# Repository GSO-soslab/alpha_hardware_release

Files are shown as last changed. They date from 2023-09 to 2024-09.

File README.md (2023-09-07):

## ALPHA HARDWARE RELEASE
This repository provides design files for ALPHA AUV hardware.
- `Electronics` folder contains KiCad PCB files, documentations and guides.
- `CAD` folder contains CAD files for the mechanical parts.

**License: CERN-OHL-S-2.0**

**Funding:** NSF Award #2221676, #2238168 and #2154901

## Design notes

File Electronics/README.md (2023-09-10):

# ALPHA Hardware Repositority

The ALPHA Eletronics Hardware design is released under  [CERN-OHL-S-2.0](https://ohwr.org/cern_ohl_s_v2.txt) Licence
## **Introduction**

The most recent update:

- `sbc_hat` is a expansion board for single-board computers. It contains 8 RS232 ports (4 selectable between UART and RS232), 2 I2C buses, 2 ADC channels, and 5 direct GPIO connections. PDF schematics is available [here](https://github.com/GSO-soslab/alpha_hardware_release/blob/main/Electronics/doc/Schematics/sbc_hat.pdf)

- `thruster_driver` is a breakout board for MCU (MicroMod RP2040). This board is designed for interface with ESCs to control the thruster and servos. The voltage sensing capability is available (using a voltage devider) to monitoring the voltage to the thrusters. Communication ports are I2C, RS232 and RS485. Two additional GPIO is available for Digital Output fucntion. PDF schematics is available [here](https://github.com/GSO-soslab/alpha_hardware_release/blob/main/Electronics/doc/Schematics/thruster_driver.pdf)
 
- `Battery management` is a breakout board that uses diodes to allow battery pack parallization upto 4 packs. **IMPORTANT: You cannot charge batter packs from the Vout port on the board**

- `alpha_power_distribution_board` is a breakout board for distributing power sources for different devices on the ALPHA. You can plug in Pololu DC/DC circuit on the board with a 90 degree angled pin headers. A PDF schematics is available [here](https://github.com/GSO-soslab/alpha_hardware_release/blob/main/Electronics/doc/Schematics/alpha_power_distribution.pdf)

The detailed hardware information is available in the following links for users.
- [PI setup guide](https://github.com/GSO-soslab/alpha_hardware_release/blob/main/Electronics/doc/PI_setup_guide.md): This document provide information on how to configure the chips on the sbc_hat PBC.

- [`sbc_hat`](https://github.com/GSO-soslab/alpha_hardware_release/blob/main/Electronics/doc/SBC_HAT.md)

- [`thruster_driver`](https://github.com/GSO-soslab/alpha_hardware_release/blob/main/Electronics/doc/Thruster_driver.md)

- [`alpha_power_distribution_board`](https://github.com/GSO-soslab/alpha_hardware_release/blob/main/Electronics/doc/Alpha_power_distribution.md).

- [`Battery management`](https://github.com/GSO-soslab/alpha_hardware_release/blob/main/Electronics/doc/Battery_management.md)

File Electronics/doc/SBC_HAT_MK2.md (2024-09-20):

Pending update

## **SBC HAT MK2**
This board was originally design to be connected to a Raspberry PI 4.
However, it should also work with other SBCs with the same GPIO pin arrangement, e.g., Nvidia Jetson SBCs.

### RS232
All the pin functinos for the connectors are indicated on the PCB.

  To enable the I2C to UART chips, you need to edit `/boot/firmware/config.txt` file by adding the following lines.
  
  ```
#RS232 1&2 
dtoverlay=sc16is752-i2c,int_pin=23,addr=0x48
  ```

### ADC ports
Pin 1&2: A0
Pin 3&4: A1
The Voltage input are stepped down using a pair of resitors of 100k and 10k.

### PWM channels
We have 15 PWM channel exposed from the `PCA9685PW` chip. 
ROS driver of the chip can be found [here](https://github.com/uri-ocean-robotics/mvp_hardware_drivers/tree/noetic-devel/pwm_driver).

***Note***
The actual PWM signal generated by the chip maybe slightly off.
We suggest to use a oscilliscope to measure the PWM output.
You can tune the `pwm_ms_bias` parameter to offset the pwm signal to match the number you commanded.

### GPIO
WE have exposed 8 GPIO pins from the PI4.
GPIO7,8,9,10,11,12,13,16
We have a driver based on wiringPi to control the GPIO [here](https://github.com/uri-ocean-robotics/mvp_hardware_drivers/tree/noetic-devel/mvp_gpio_manager)

***Note1:***
The gpio param in the driver is based on the WiringPi pin map.
GPIO7 = 11
GPIO8 = 10
GPIO9 = 13
GPIO10 = 12
GPIO11 = 14
GPIO12 = 26
GPIO13 = 23
GPIO16 = 27

***Note2:***
You can program the gpio initial state to low by adding the commands in `/boot/firmware/config.txt`
```
gpio=13=op,dl
```
where `13` is the GPIO number (not the WiringPi number).

***Note3:***
Continous command from PI is not needed. The PWM will hold the PWM signal based on the last received command.

### MCU
We have a place for soldering a ATtiny85-20P MCU.
The MCU's I2C bus is connected to the PI's I2C, and `PB1` is connected to the `Enable` Pin of the PWM chip.
This allows user to implement safety feature to let MCU to turn off the PWM chip when no data is transmitted from PI to MCU.

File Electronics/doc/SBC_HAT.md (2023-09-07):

## **SBC HAT**
This board was originally design to be connected to a Raspberry PI 4.
However, it should also work with other SBCs with the same GPIO pin arrangement, e.g., Nvidia Jetson SBCs.

All the pin functinos for the connectors are indicated on the PCB.

  To enable all 4 I2C to UART chips, you need to edit `config.txt` file by adding the following lines.
  
  ```
#RS232 1&2 
dtoverlay=sc16is752-i2c,int_pin=23,addr=0x48
#RS232 3&4
dtoverlay=sc16is752-i2c,int_pin=24,addr=0x4C
#RS232 5&6 
dtoverlay=sc16is752-i2c,int_pin=25,addr=0x49
#RS232 7&8
dtoverlay=sc16is752-i2c,int_pin=22,addr=0x4D
  ```
  The port and connector index is listed below

  J14 = ttySC6

  J15 = ttySC7
  
  J9 = ttySC4
  
  J10 = ttySC5
  
  J4 = ttySC2
  
  J5 = ttySC3
  
  J8 = ttySC1
  
  J7 = ttySC0

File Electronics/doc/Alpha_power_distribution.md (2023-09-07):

## **ALPHA Power distribution board**

This board is designed to distribute the input voltage for different systems on the ALPHA AUV.
- The terminal blocks are rated at 16A. This is good for thrusters, input battery lines, and other high current draw sensors.
- The JST-XH connector are rated at 3A. This is designed for mid-low power sensors. 
- There are several JST-XH outputs 5v and 12v as indicated on the board. 
   - `5V3`, `5V2` and `5V1` obtains 5V power from different `D36V28F5` DC/DC regulator (5-50v input range with a max current rating of 3.2A) 
   - `12v` ports obtain power from a `D36V50F12` (5-50v input range with a maximum current rating of 4.5A)
   - Qwiic connector pins are connected to the enable pin of the `D36V50F12`, `D36V28F5`. 
      - Pin 1 controls 5V1 from U1
      - Pin 2 controls 5V2 from U2
      - Pin 3 controls 5V3 from U3
      - Pin 4 controls 12V from U4

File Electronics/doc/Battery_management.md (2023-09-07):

## **Battery power distribution board
This board is used to parallelize upto four battery packs to supply continuous energy for the ALPHA.

- Two rectifier diode arrays can be soldered (1 pair common cathode). We recommend to use `FERD60H100CGY-TR` which is rated at 100 V at 30A per diode. Or you can use `RB238NS150FHTLCT-ND` which is rated at 150v at 20A per diode.
- The diodes allows us to parallel multiple packs without charge each other. However, the downside is that only one battery pack (with the highest voltage) is supplying the energy to the overall system. Therefore, you need make sure the following things:
   - The battery's maximum discharge current rating is enough for your system
   - Your wiring for each battery is sufficient for carrying all the current.
- All the pads on the top layer are Positive pin of the battery or the output power. VB1 to VB4 pads are enlarged to allow two wires to be soldered on each pad. One wire connects to the battry, one wire connects to the charger.
- All the pads on the bottom layer are GND pads.

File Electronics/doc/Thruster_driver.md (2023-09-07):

## **Thruster driver board**
  ### Power input
  - The board can only be powered by 3.3v at `J8`
  
  ### Programming the MicroMod RP2040
  - Connect the two pins at `J11` to set the board to the boot mode before powering the system and connect the USB cable at `J10` 
  - Getting started document can be found [here](https://datasheets.raspberrypi.com/pico/getting-started-with-pico.pdf)
  - RP2040 SDK is can be found in [pdf](https://datasheets.raspberrypi.com/pico/raspberry-pi-pico-c-sdk.pdf) or [web](https://raspberrypi.github.io/pico-sdk-doxygen/)
  - Pin map of the MicroMod RP2040  can be found [here](https://learn.sparkfun.com/tutorials/micromod-rp2040-processor-board-hookup-guide), and pin map of RP2040 is available [here](https://datasheets.raspberrypi.com/pico/Pico-R3-A4-Pinout.pdf)
  - The actual Pin number for the PWM ports and the Serial ports are listed in the following section.
  - `J12` is used for reset the board.

  ### Building pico code inside the build/xx folder
  ```
      mkdir build
      cd build
      cmake ..
      make hello_pio
   ```

  ### Function ports
  - RS232-1 (4pin JST): the uart0 (GP0-TX, GP1-RX on RP2040) is converted into a RS232 port at `J7`. 
    - Pin1 (white bar): GND
    - Pin2: 3.3V from the power
    - Pin3: TX
    - Pin4: RX

 - RS232-2 (4pin JST): the uart1 (GP8-Tx, GP9-Rx on RP2040) into RS232 at `J2`. 
    - Pin1 (white bar): GND
    - Pin2: 3.3V from the power
    - Pin3: TX
    - Pin4: RX

 - I2C (4pin JST): The board has one I2C communication port at `J5`. 
    - Pin1: GND
    - Pin2: 3.3V
    - Pin3: SDA (GP04 on RP2040)
    - Pin4: SCL (GP05 on RP2040)

- PWM channels (4pin JST): The board has 6 PWM channels at `J3`, `J4` and `J6` for controlling ESC and servo motors.
    - Pin1&2: GND
    - Pin3&4: PWM signal
    - J3: P3->GPIO24->4A, P4->GPIO13->6B
    - J4: P3->GPIO18->1A, P4->GPIO16->0A
    - J6: P3->GPIO22->3A, P4->GPIO20->2A
    - These pins could be configured as regular GPIO as well.

- Voltage sensing (VB at `J8`). User could sense the input voltage at VB pin through a voltage divider (100k omh and 10k omh in serial). The divided voltage is connected to GPIO26(ADC0) on the RP2040.

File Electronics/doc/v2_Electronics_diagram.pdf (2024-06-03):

Power distribution board

VB

5V

12V

MCU
board
PWM | RS232
USB | Pi4 with HAT
Ethernet | RS232

I2C

ADC

VIN

VIN

VIN

LUMA_E

VIN

Current sensor Analog Out

MB switch

VIN Tether Tether board

ESC

VIN

PWM

Motor wires VIN

PWM

Motor wires VIN

PWM

Motor wires VIN

PWM

Motor wires

VB | VB Current through

5V

Ethernet FLS_3 Ping360_E

Doodle_E

Ethernet

5V

VB

VB

VB

Surge¹ | VB

Sway¹,2

HS¹,2

# HB¹,2 Vin

Acomm

# WIFI GPS Tether

Ping
360³

Bar30

DVL³

FLS³

VB

VB

24v

24v

3 pin | 4 pin

6 pin Hybrid New

6pin
hybrid
old

8 pin
old

8 pin New

Note 1: All thruster should use the same blade direction. And the motor wiring has to be confirmed such that PWM >1500 will generate thrust towards the cable side (air pushing through the thruster). Note 2: T200 Thrusters on ALPHA RISE uses 3pin-power connector, which is thicker than the regular BT 3pin connector Note 3: All ethernet port are powered by VB unless further described. Note 4: Dotted line means additional devices

# PWM0 PWM1 PWM2 PWM3

VB

RS232-1

ttySC3
J5
J4/ttySC2 Ethernet Standard BT Bulkhead connector wiring 1 | RX+ 2 | RX- 3 | TX+ 4 | Vcc 5 | GND 6 | TX- 78 | Serial RX or IO
Cable (Female) | Bulkhead (Male) | Tether 1 | NC 2 | NC 3 | NC 4 | + 5 | - 6 | NC 7 | NC 8 | NC | 1 | D1- 2 | D1+ 3 | D2- 4 | D3+ 5 | D3- 6 | D2+ 7 | 5V 8 | GND Triple USB (Old Fin) 1 | D1- 2 | D1+ 3 | 5V2 4 | D2+ 5 | D2- 6 | 5V1 7 | GND2 8 | GND1
Double USB (WIFI+GPS Fin)
Ethernet 1 | GND 2 | VCC 3 | RX+ 4 | RX- 5 | TX+ 6 | TX-

## Bulkhead (Male)

Serial TX or IO

Cable (Female) | 1 | GND 2 | 5V 3 | D- 4 | D+ 5 | D- 6 | D+
Double USB (WIFI+GPS Fin) | 1 | GND 2 | 5V 3 | D- 4 | D+ 5 | SBC_RX 6 | SBC_TX

USB + RS232

Cable (Female) | Bulkhead (Male) | RS232 1 | GND 2 | VCC 3 | SBC_RX 4 | SBC_TX
Main power 1 | GND 2 | VB 3 | GND 4 | VB
Battery power (customized with BR 12 AWG Power cable) 1 | GND 2 | GND 3 | VB 4 | VB
Servo/LED 1 | GND 2 | VCC 3 | PWM
Cable (Female) | Bulkhead (Male)

Double USB Main power Tether

Ethernet

Ethernet

Ethernet

RS232

Battery1

Battery2

Battery3

Battery4

Dual diode

Dual diode

Battery power

Battery power

Battery power

Battery power

VIN | GND
Main power 1 | GND 2 | 5V 3 | D- 4 | D+ 5 | NC 6 | Sync (optional)

Single USB

## Battery management diagram

## Electronics housing

## 12A rated per pin

## 20A rated per pin

## 20A (P1 & P2) 3A (P3-P6)

## 3A per pin

## Connector color code

VIN Tether_E

GB Switch

Ethernet

Jetson E

DVL_E

PI_E

VB

LUMA³

Long
range WIFI³

Jetson Ethernet USB

USBX2

USB Camera USB

3.0

PWM | LED

VIN

PWM

Motor wires

VIN

PWM

Motor wires

Thruster
/Servo

Thruster
/servo

12v 12v

30 A rated per channel

6pin
regular

GPIO13

ADC1

ADC0 1 | NC 2 | SSTX+ 3 | SSTX- 4 | SSRX+ 5 | SSRX- 6 | D+ 7 | D- 8 | NC

USB3

Cable (Female) | Bulkhead (Male) | 1 | GND 2 | 5V 3 | Pri Exposure 4 | Pri Trigger 5 | Sec Power 6 | Sec. Exposure

FLIR Cam
power +trigger

VIN

12v

DVL_E

LUMA-E 1 | B- 2 | B+ 3 | B1 4 | B3 5 | B2 6 | NC

BR 14.8V battery balance port

Latte Panda USB USB USB | IP | HDMI

Power

VIN

Ethernet

GB Switch

Ethernet

Ethernet

Ethernet

Ethernet

Internet

Router Ethernet VIN

Ethernet Acomm | USB

HDMI

Power bar VVVV | Power

USB Keyboard

Mourse

Long range WIFI

IP

Power

Internet

Antenna | Antenna

Front

Bottom Top
Back

Back

BackTop | Text Tether_E | Doodle_E | GPS

Antenna Tether board

TP-link N300

TP-link N300 | Laptop

Laptop

5km Tether port 1 | BLK-1 2 | RED-1 3 | Y-1 4 | BLK-2 5 | RED-2 6 | Y-2

ESC spliter

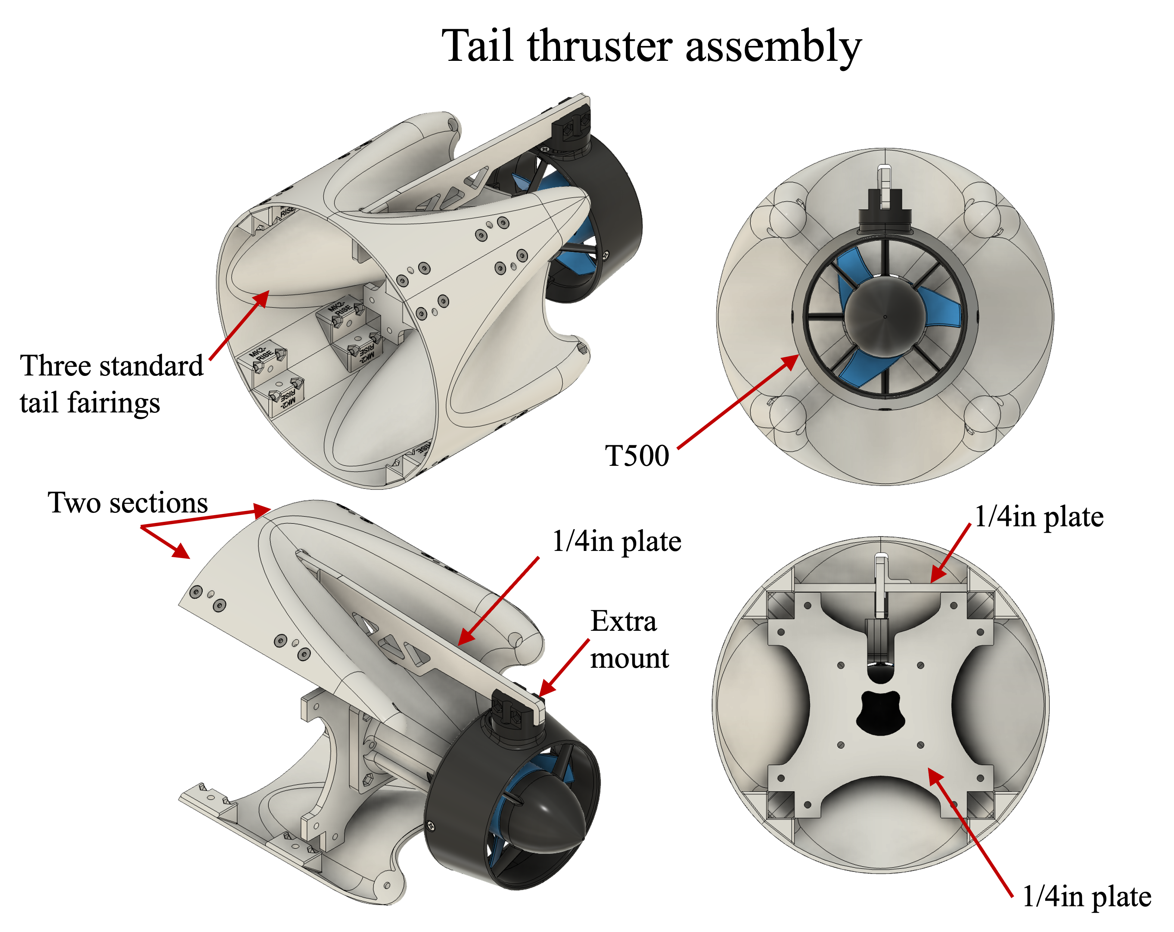
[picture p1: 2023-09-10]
CAD/Acutators/AC-AS-01-02.png

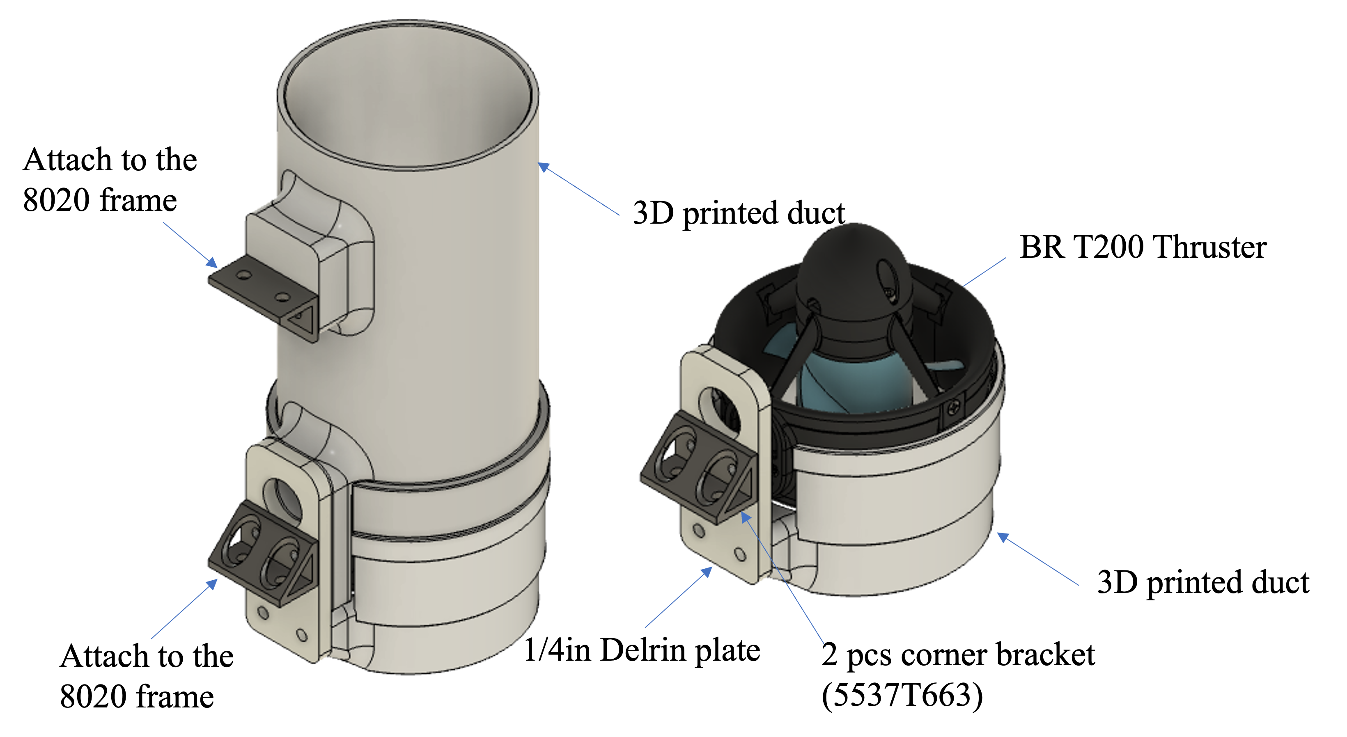
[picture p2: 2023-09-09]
CAD/Acutators/AC-AS-01-01.png

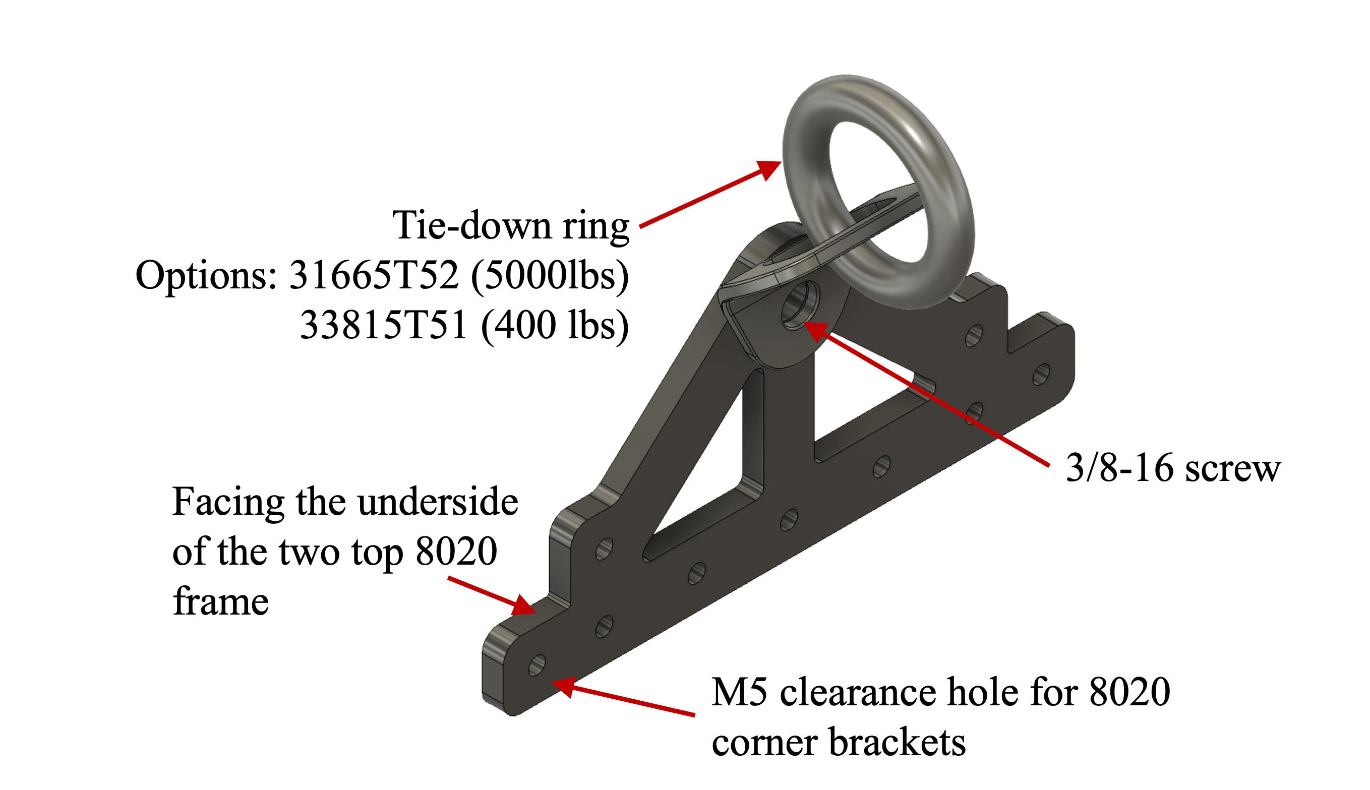
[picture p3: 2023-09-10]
CAD/Others/Lifting_plate_diagram.png

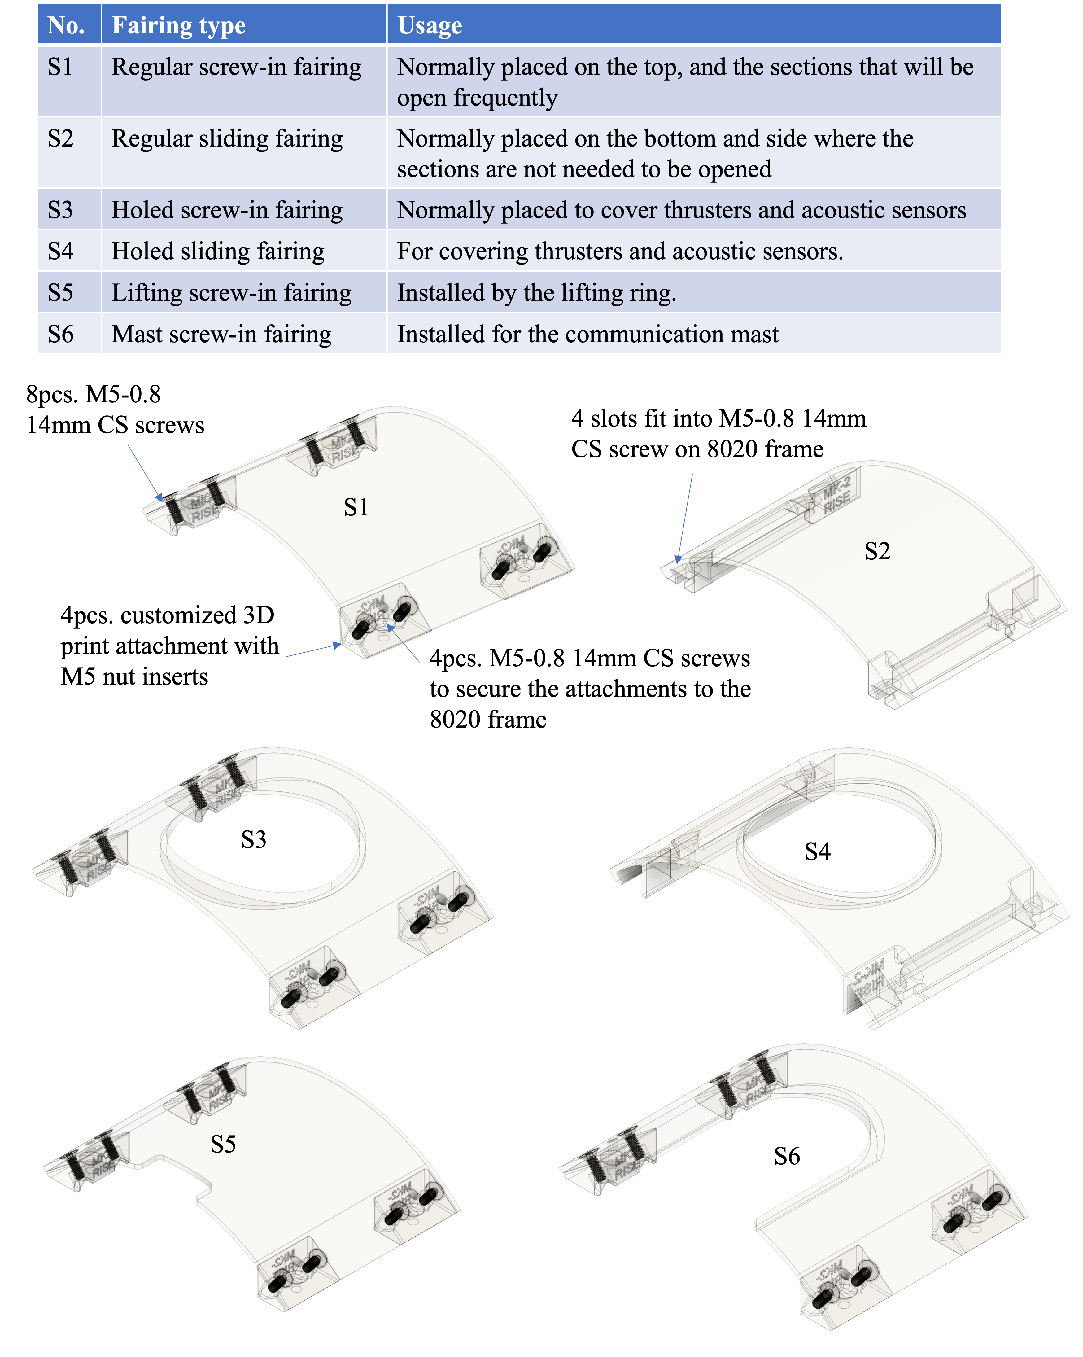
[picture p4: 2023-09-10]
CAD/Fairing/fairing_information.png

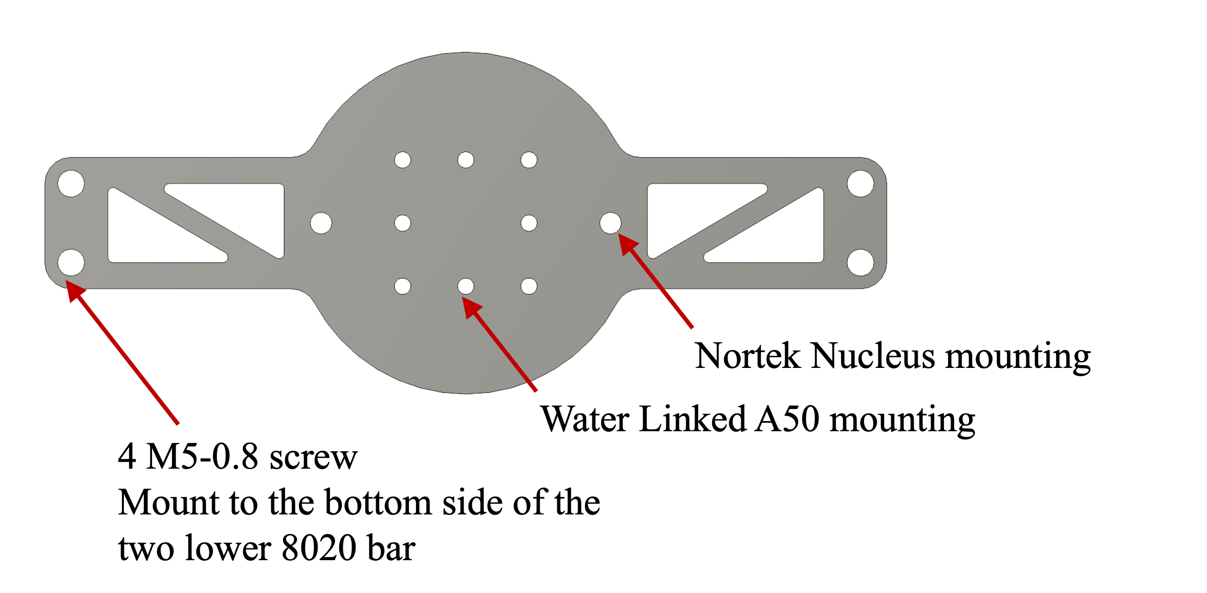
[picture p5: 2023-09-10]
CAD/Others/DVL_plate_information.png

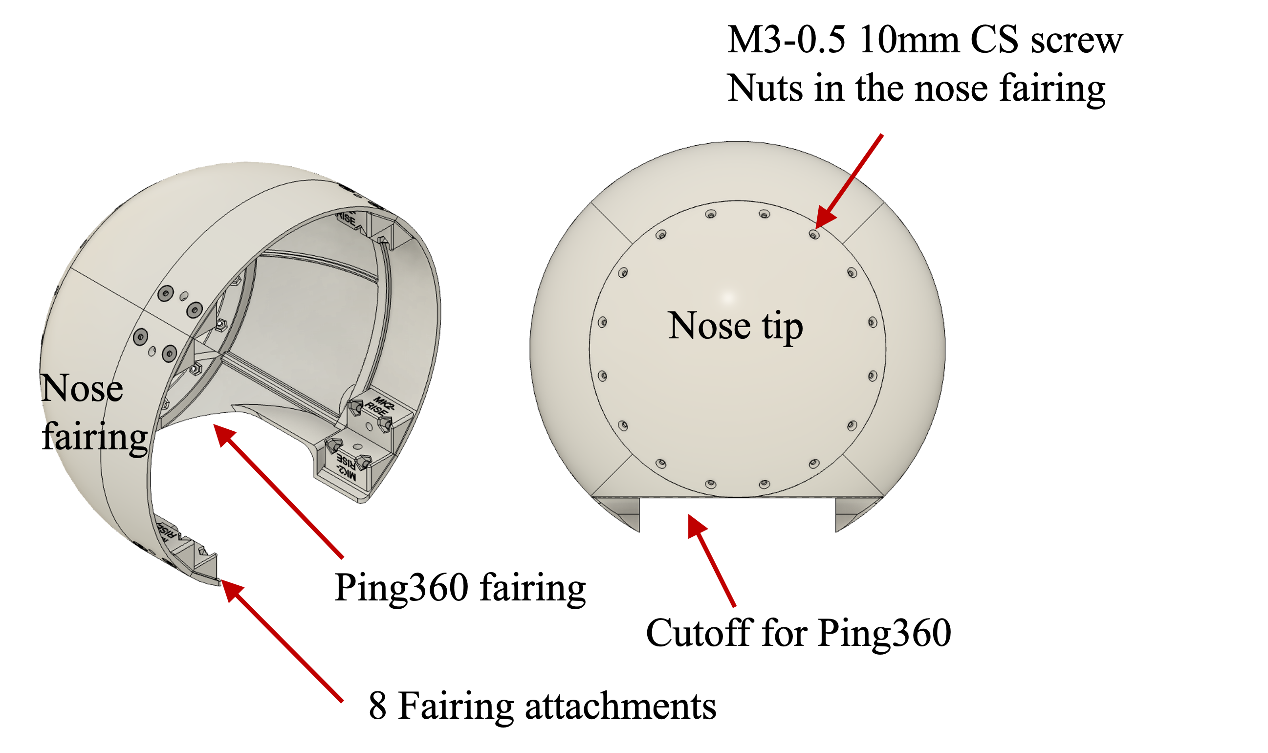
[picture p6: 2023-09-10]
CAD/Fairing/FA-AS-01-01.png

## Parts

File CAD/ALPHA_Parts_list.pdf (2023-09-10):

ALPHA Parts List

Part number explaination
XX-XX-XX-XX
1st and 2nd digits Category | BR-Blue Robotics, MC-McMaster Carr
3rd and 4th digits Assembly | External vendor uses vendor part number and description
5th and 6th digits | Assembly number
7th and 8th digits | Number | 00 means an assembly
Category | Part number | Description
Actuators (AC) | AC-AS-01-00 | Tunnel thruster assembly
Actuators (AC) | AC-AS-01-01 | Short tunnel
Actuators (AC) | AC-AS-01-02 | Long tunnel
Actuators (AC) | BR-T200 | Blue Robotics T200
Actuators (AC) | MC-5537T663 | T-slot corner bracket 2 holes
Actuators (AC) | AC-AS-02-00 | Surge thruster assembly
Actuators (AC) | AC-AS-02-01 | T500 Top mount
Actuators (AC) | AC-AS-02-02 | T500 Back mount
Actuators (AC) | AC-AS-02-03 | T500 Mounting plate
Actuators (AC) | AC-AS-02-04 | T500 hanging plate
Actuators (AC) | AC-AS-02-05 | T500 hanging cross
Actuators (AC) | BR-T500-R1 | Blue Robotics T500
Electronics (EL) | EL-AS-01-00 | Electronics housing assembly (4in aluminum Blue Robotics Housing)
Electronics (EL) | EL-AS-01-01 | Internal chasis end plate
Electronics (EL) | EL-AS-01-02 | Internal electronics mounting plate
Electronics (EL) | BR-STANDOFF | Blue Robotics M3 standoff 212 mm long
Fairing (FA) | FA-AS-01-00 | Nose cone fairing assembly
Fairing (FA) | FA-AS-01-01 | Nose fairing
Fairing (FA) | FA-AS-01-02 | Nose fairing for Ping360
Fairing (FA) | FA-AS-01-03 | Nose tip fairing
Fairing (FA) | FA-AS-02-00 | Tail cone fairing assembly
Fairing (FA) | FA-AS-02-01 | Tail cone fairing regular
Fairing (FA) | FA-AS-02-02 | Tail cone fairing top port
Fairing (FA) | FA-AS-02-03 | Tail cone fairing top starboard
Fairing (FA) | FA-AS-03-00 | Mid section fairing assembly
Fairing (FA) | FA-AS-03-01 | Screw-in fairing regular
Fairing (FA) | FA-AS-03-02 | Slide-in fairing regular
Fairing (FA) | FA-AS-03-03 | Screw-in fairing for thruster/DVL
Fairing (FA) | FA-AS-03-04 | Slide-in fairing for thruter/DVL
Fairing (FA) | FA-AS-03-05 | Screw-in fairing for lifting plate
Fairing (FA) | FA-AS-03-06 | Screw-in fairing for mast
Fairing (FA) | FA-00-01 | Screw-in fairing adapter
Frame (FR) | FR-AS-01-00 | ALPHA main frame
Frame (FR) | FR-AS-01-01 | Big middle frame 1/2in HDPE
Frame (FR) | FR-AS-01-02 | Small middle frame for holding housings 1/2in HDPE
Frame (FR) | FR-AS-01-03 | Special screw-in fairing adapter
Frame (FR) | MC-5537T935 | 20mm 8020 Corner bracket
Frame (FR) | MC-5537T518 | 20mm 8020 Corner bracket
Frame (FR) | MC-5537T514-4FT | 4ft long 20mm 8020
Stand (ST) | ST-AS-01-00 | AUV Stand Assembly
Stand (ST) | ST-AS-02-00 | Stand Arc assembly
Stand (ST) | ST-AS-01-01 | Arc plate
Stand (ST) | ST-AS-01-02 | 3D Printed Arc core side
Stand (ST) | ST-AS-01-03 | 3D Printed Arc core middle
Stand (ST) | MC-47065T107 | 1in by 2in 8020 3ft or 4ft long
Stand (ST) | MC-47065T101 | 1in by 1in 8020 6in long
Stand (ST) | MC-47065T663 | 1in 8020 corner bracket
Others (OT) | OT-AS-01-01 | DVL plate 1/4in thick Delrin
Others (OT) | OT-AS-02-01 | Lifting plate 1/4 in Aluminum
Others (OT) | MC-33815T51 | Lifting ring 400 lbs rated
Others (OT) | MC-31665T52 | Lifting ring 5000 lbs rated
Others (OT) | OT-AS-03-00 | Ping360 mounting assembly
Others (OT) | OT-AS-03-01 | Ping360 Plate 3/16in Delrin
Others (OT) | OT-AS-03-02 | Ping360 Spacer, 3D printed
Others (OT) | BR-Ping360 | Blue Robotics Ping360

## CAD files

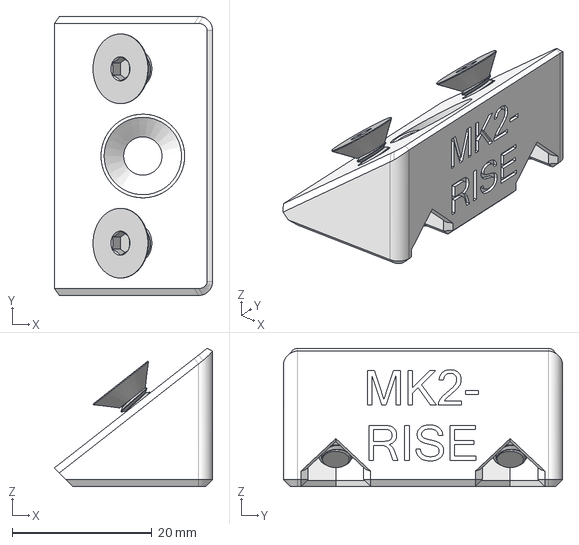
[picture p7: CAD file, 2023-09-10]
CAD/Fairing/Parts/FA-00-01.step
22.7 x 40.0 x 19.8 mm
92125A211_18-8 Stainless Steel Hex Drive Flat Head Screw x 2

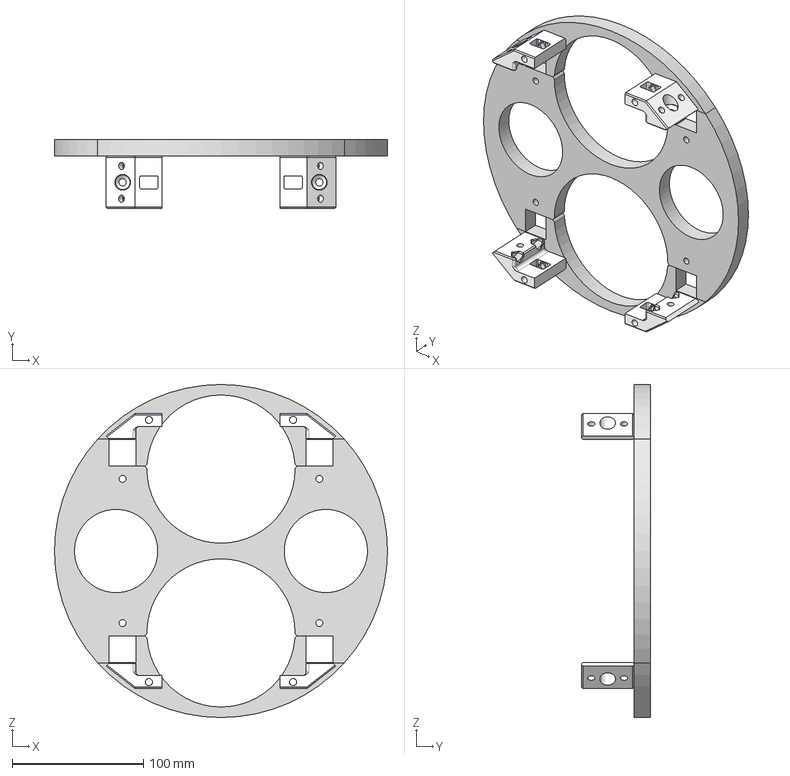
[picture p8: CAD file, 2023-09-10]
CAD/Frame/FR-AS-02-00.step
254.0 x 52.7 x 254.0 mm
FR-AS-01-01
FR-AS-01-02 x 2
FR-AS-01-03 x 2
FR-AS-01-03 v1(Mirror) x 2

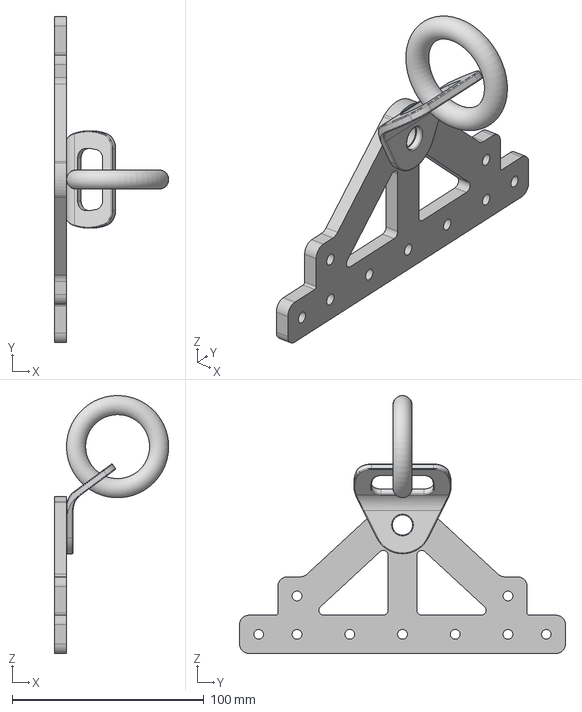
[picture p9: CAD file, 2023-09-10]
CAD/Others/Parts/OT-AS-02-00.step
59.7 x 170.0 x 134.5 mm
OT-AS-02-01
MC-31665T52

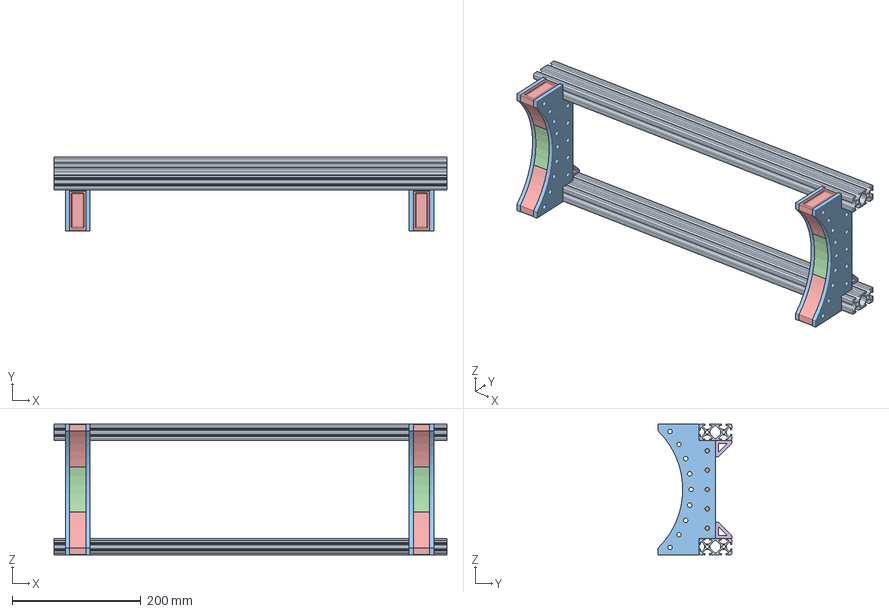
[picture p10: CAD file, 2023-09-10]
CAD/Stand/ST-AS-01-00 v2.step
609.6 x 114.3 x 203.2 mm
MC-47065T107 x 2
MC-47065T411_6in x 2
ST-AS-01-01 x 4
ST-AS-01-03 x 2
ST-AS-01-02 x 4
MC-47065T663 x 4

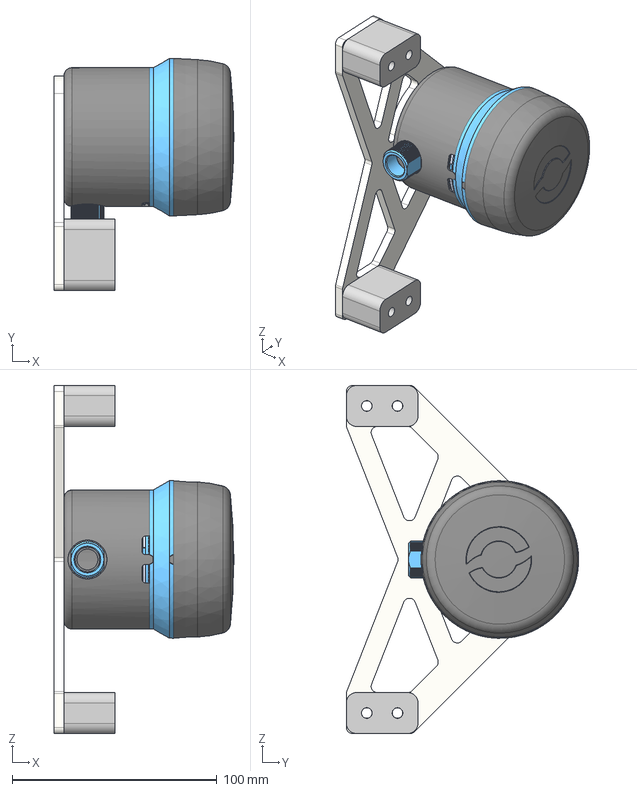
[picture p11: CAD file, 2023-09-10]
CAD/Others/Parts/OT-AS-03-00.step
87.8 x 113.5 x 170.0 mm
OT-AS-03-01
OT-AS-03-02 x 2
BR-Ping360

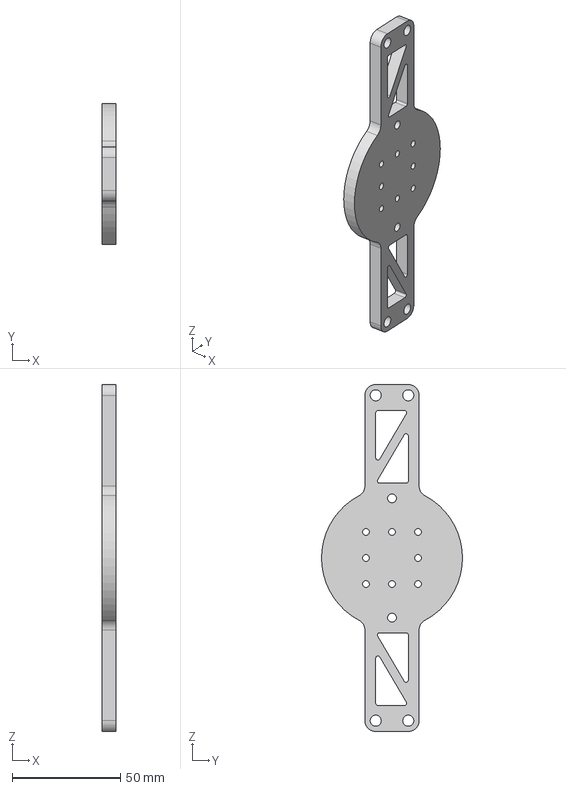
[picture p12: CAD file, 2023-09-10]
CAD/Others/Parts/OT-AS-01-01.step
6.35 x 65.0 x 160.0 mm

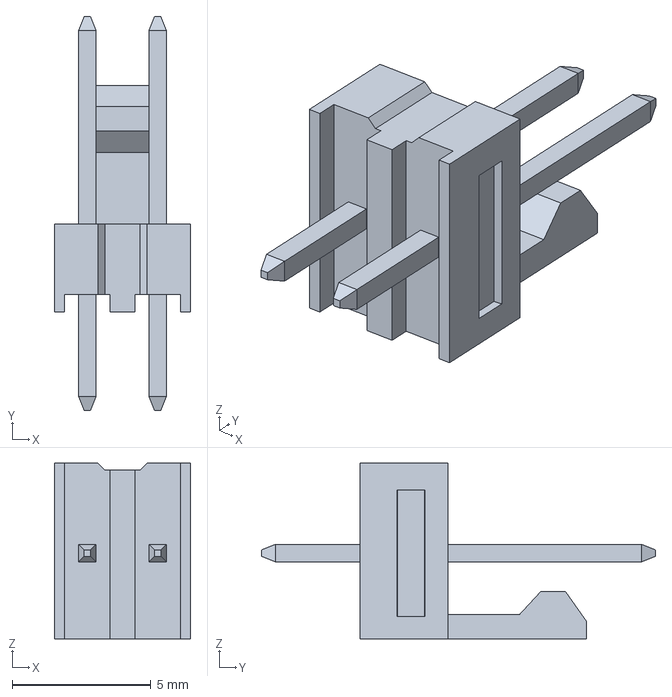
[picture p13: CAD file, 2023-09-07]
Electronics/sbc_hat_mk2/project_3dshapes/022232021.stp
4.93 x 14.2 x 6.35 mm

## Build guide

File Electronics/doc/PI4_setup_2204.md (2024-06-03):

### First-time boot-up setup (HDMI and keyboard needed)

- username: `mvp_admin`, password: `temppwd`

- `hostname -I` or `ip -a address` to check current IP
- Edit the netplan `sudo nano /etc/netplan/50-cloud-init.yaml`
- add `addresses: [192.168.1.124/24]`
- `ping google.com`
- Disable auto update `sudo dpkg-reconfigure -plow unattended-upgrades`

### Open I2C port

- `sudo apt update`
- `sudo apt install raspi-config`
- `sudo raspi-config`
- Go to `Interface Options` > `I2c` enable it
- Go to `Interface Opetions` > `SPI` disable it

### Setup I2C UART Chip (sc16is752-i2c)

- Install libraries

  ```
  sudo apt-get install -y make
  sudo apt-get install build-essential
  ```

  ```
  wget http://www.airspayce.com/mikem/bcm2835/bcm2835-1.71.tar.gz
  tar zxvf bcm2835-1.71.tar.gz 
  cd bcm2835-1.71/
  sudo ./configure
  sudo make
  sudo make check
  sudo make install
  #For more details, please refer to http://www.airspayce.com/mikem/bcm2835/
  ```

  ```
  sudo apt-get install python3-dev
  sudo apt-get install python3-rpi.gpio
  sudo apt-get install python3-smbus
  ```

- Add device using `dtoverlay`

  - `sudo nano /boot/firmware/config.txt`

  - add the following lines at the end

    ```
    #RS232 1&2 SC6, SC7
    dtoverlay=sc16is752-i2c,int_pin=23,addr=0x48
    #RS232 3&4 SC4, SC5
    dtoverlay=sc16is752-i2c,int_pin=24,addr=0x4C
    ##the last two is for the 8 RS232 version
    #RS232 5&6 SC2 SC3
    dtoverlay=sc16is752-i2c,int_pin=25,addr=0x49
    #RS232 7&8 SC0 SC1
    dtoverlay=sc16is752-i2c,int_pin=22,addr=0x4D
    ```

  - `sudo reboot`

- Check new serial ports

  - `ls /dev/ttySC*`

  - If you see SC0, SC1 ..... and so on, then you are good.

    | Connector | Dev    |
    | --------- | ------ |
    | J8        | ttySC0 |
    | J7        | ttySC1 |
    | J4        | ttySC2 |
    | J5        | ttySC3 |
    | J9        | ttySC4 |
    | J10       | ttySC5 |
    | J14       | ttySC6 |
    | J15       | ttySC7 |

  - Test with `minicom`

  - `sudo minicom -s`
    - `ctrl+A` then `o`: configure the port
    - `ctrl+A` then `x` : exit the program.

### GPIO conifguration 

On the hat we have 5 GPIOs (7,8, 9, 12, 13). We use the GPIO as output pins to control MOSFET and power supplies to control sensor payloads. GPIO9, 12, 13 can be configured as normal GPIO.

- First, you need to export the GPIO

```
echo 9 > /sys/class/gpio/export
```

- Second, you can set the direction of the GPIO

```
echo out > /sys/class/gpio/direction
```

- Finally, you can set the GPIO to High[1] or Low [0]

```
echo 1 > /sys/class/gpio/direction
```

***Note***: For GPIO7  and GPIO8, they are originally used as chip select pin for SPI in the PI system. To free them to become a regular GPIO, you need to add the  following line in `/boot/config.txt` and `/boot/firmware/config.txt` file after the line `dtparam=spi=off`. The added line will remapp the chip select pin to other GPIOs, i.e., 20 and 21 here. Then, you can reboot the PI, and `GPIO7` and `GPIO8` can be used as normal GPIOs.

```
dtoverlay=spi0-cs,cs0_pin=20,cs1_pin=21
```

### Install ROS Humble

[Reference](https://docs.ros.org/en/humble/Installation/Ubuntu-Install-Debians.html)

- add source bash into your ~/.bashrc 

- only install the base `sudo apt install ros-humble-ros-base`

- install the demo_node packages to test ros 

  ```
  sudo apt install ros-humble-demo-nodes-cpp
  sudo apt install ros-humble-demo-nodes-py
  ```

### Test ADC chip (MCP3422)

### Test Bar30 pressure sensor

### Test XSense MTI 

## PWM Driver add-on Board

### Configure Real-time clock (DS3231)

- Install `i2c-tools`
- `i2cdetect -y 1` to scan the device on the i2c bus and get their address
- scan the port make sure the devices are there.
- The I2C address of the clock should be `0x68`

[Reference](https://learn.adafruit.com/adding-a-real-time-clock-to-raspberry-pi/set-up-and-test-i2c)

### Configure the PWM chip (PCA9685)

- The I2C address should be `0x40` and `0x70`, the later one is the default all channel address.

## Install MVP Framework

### MVP messages

### MVP Control

### MVP Mission

### MVP Core (ALPHA_core for ROS Noetic)

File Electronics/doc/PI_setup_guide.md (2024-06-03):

# PI setup guide for the ALPHA RISE SBC HAT
## Create Ubuntu 20.04 image.
- Open **Raspberry Pi Imager** 
- Choose **Other general-purpose OS** 
- Select **Ubuntu**
- Scroll down **Ubuntu Server 20.04.5 LTS(64-bit)** option
- Click the Advanced options icon at the right-bottom corner
    - Check **Set hostname**
    - Check **Enable SSH**, select **Use password authentication**
    - Check **Set username and password**, type in the username and password you want for ssh login later on. For example, username: `alpha`, password: `temppwd`.
    - Check **Configure wireless LAN**, type in the network name and password in **SSID** and **Password**, Select the corresponding **Wireless LAN country**
    - **Save** once finished.
- Select the SDCard, then **write** the image.

## First time booting up
- Get a micro-HDMI cable to connect the PI to a monitor
- Get a usb keyboard to connect to the PI's usb.
- Plug in the power
- Login using the username and password you set.
- Network setup:
    - Setup a static IP for wifi:
        - `sudo nano /etc/netplan/50-cloud-init.yaml`
        - add changes: wifi replace encrypt-password
        ```yaml
        network: 
            version: 2
            wifis:
                renderer: networkd
                wlan0:
                    access-points:
                        soslab:
                            password: encrypt-password 
                    dhcp4: no 
                    addresses: [192.168.1.111/24]
                    nameservers:
                        addresses: [192.168.1.1, 8.8.8.8]
                    gateway4: 192.168.1.1
        ```
        - apply the changes:
        ```shell
        sudo netplan generate
        sudo netplan apply
        sudo reboot
        ```
    - Enable netowrk for Fin(USB wifi) and Ethernet:
        - `sudo nano /etc/netplan/50-cloud-init.yaml`
        - add changes: comment out `wlan0` for the original PI wifi
        ```yaml
        network:
        version: 2
        wifis:
            renderer: networkd
            #wlan0:
            #    access-points:
            #        soslab:
            #            password: encrypt-password 
            #    dhcp4: no 
            #    addresses: [192.168.1.111/24]
            #    nameservers:
            #        addresses: [192.168.1.1, 8.8.8.8]
            #    gateway4: 192.168.1.1
            wlan1:
                access-points:
                    soslab:
                        password: encrypt-password 
                dhcp4: no 
                addresses: [192.168.1.121/24]
                nameservers:
                    addresses: [192.168.1.1, 8.8.8.8]
                gateway4: 192.168.1.1
        ethernets:
            eth0:
                dhcp4: no 
                addresses: [192.168.2.121/24]
        ```
        - apply same changes
        ```sh
        sudo netplan generate
        sudo netplan apply
        sudo reboot
        ```
    - type `hostname -I` or `ip -a address`, you should see the new IP of your PI now.

    - Note: if you want to use ethernet port on the PI to access internet, you need to comment out `nameservers` and `gateway4` line under `wlan1` and add proper address under `eth0` 

- You can disable the auto update:
    ```
    sudo dpkg-reconfigure -plow unattended-upgrades
    ```
## Test the USB Hub
- You can solder the jumper JP1 to power the USB Hub chip. The middle pad is connected to the USB Hub Vcc, the one with an arrow is the pad connected to 5V PI input, and the other one is connected to the USB upstream 5v. For teting your can solder the USB Hub Vcc to the upstream power.
- Use a micro usb cable to plug into the upstream usb port. 
- Plug in any USB device to other ports. You should be able to see the device if the board is working. Meanwhile, you should see LEDs are on to indicate a device is detected on a port.

## USB device udev rules
- For GPS:
    - find usb port: 
    ```sh
    dmesg | greb cp210
    ```
    - find device information: 
    ```sh
    # replace the # with your usb device number
    sudo udevadm test $(udevadm info -q path -n /dev/ttyUSB#) 
    ```
    - generate udev rules: may has conflict with gpio, check [reference](https://github.com/raspberrypi/linux/issues/3989)
    ```sh
    # replace idVendor and idProduct from last step
    sudo bash -c 'echo "SUBSYSTEM==\"tty\", ACTION==\"add\", ATTRS{idVendor}==\"10c4\", ATTRS{idProduct}==\"ea60\", SYMLINK+=\"alpha_gps\"" > /etc/udev/rules.d/99-usb-gps.rules'
    ```
    - reboot to enable rules
    - check SYMLINK: `ls -l /dev/alpha_gps`
- For RF:
    - find us port:
    ```sh
    dmesg | greb ch341
    ```
    - find device information: 
    ```sh
    # replace the # with your usb device number
    sudo udevadm test $(udevadm info -q path -n /dev/ttyUSB#) 
    ```
    - generate udev rules:
    ```sh
    # replace idVendor and idProduct from last step
    sudo bash -c 'echo "SUBSYSTEMS==\"usb\", ACTION==\"add\", ATTRS{idVendor}==\"1a86\", ATTRS{idProduct}==\"7523\", SYMLINK+=\"alpha_rf\"" > /etc/udev/rules.d/99-usb-rf.rules'
    ```
    -  reboot to enable rules
    -  check SYMLINK: `ls -l /dev/alpha_rf`
  
## Raspi-config ##
If you are using Ubuntu you may not have raspi-config for enabling ports for the PI.
You can simply type `sudo raspi-config` in the terminal to see if you have it or not.

If you don't have it, you can following the instruction here to install it.
```
wget https://archive.raspberrypi.org/debian/pool/main/r/raspi-config/raspi-config_20200601_all.deb -P /tmp
sudo apt-get install libnewt0.52 whiptail parted triggerhappy lua5.1 alsa-utils -y
# Auto install dependancies on eg. ubuntu server on RPI
sudo apt-get install -fy
sudo dpkg -i /tmp/raspi-config_20200601_all.deb
```

## Enable and test I2C ports
- Open a terminal and type in 
```sudo raspi-config ```
- In the window, choose Interfacing Options -> I2C ->yes 
- Reboot the PI, ```sudo reboot```
- You can plug-in a I2C device, e.g., the [pressure sensor](https://bluerobotics.com/store/sensors-sonars-cameras/sensors/bar30-sensor-r1/) from Blue Robotics. And use the [python script](https://github.com/bluerobotics/ms5837-python) to validate if your PI can talk to the sensor.

## Enable the I2C to dual UART ICs and test RS232 ports
The original instruction is available here from [waveshare](https://www.waveshare.com/wiki/Serial_Expansion_HAT). The major change is the use of `python3` prefix and the way we edit the `config.txt` for Ubuntu image.
Our RS232 Ports are created from the I2C bus. If you have enabled I2C in the above step, you don't have to enable it again.
- Install make and build
```
    sudo apt-get install -y make
    sudo apt-get install build-essential
```
- Install libraries
```
wget http://www.airspayce.com/mikem/bcm2835/bcm2835-1.71.tar.gz
tar zxvf bcm2835-1.71.tar.gz 
cd bcm2835-1.71/
sudo ./configure
sudo make
sudo make check
sudo make install
#For more details, please refer to http://www.airspayce.com/mikem/bcm2835/
```
- Install WiringPi libraries
```
sudo apt-get install wiringpi

#For Pi 4 with Pi OS image, you need to update it：
cd /tmp
wget https://project-downloads.drogon.net/wiringpi-latest.deb
sudo dpkg -i wiringpi-latest.deb
gpio -v
#You will get 2.52 information if you install it correctly
```
- **IMPORTANT: Ubuntu user**
    - Download the release from `https://github.com/WiringPi/WiringPi/releases`. Make sure you used the `-arm64.deb` version
    - copy from your local computer to the Pi use `scp`, then install it.
        ```
        scp wiringpi-2.61-g.deb alpha@192.168.1.110:
        sudo dpkg -i wiringpi-latest.deb`
        gpio -v
        ```

- Install python packages (you need to use `python3` prefix if you are using python3)
```
sudo apt-get install python3-dev
sudo apt-get install python3-rpi.gpio
sudo apt-get install python3-smbus
```

- Configure the I2C to UART IC
    - Edit the boot/config.txt (**for Ubuntu, you can directly edit the config.txt in the SD Card, the edit in /boot/config.txt won't work**)
        ```
        sudo nano /boot/firmware/config.txt
        ```
    - Add the following line at the end
        ```
        #RS232 1&2 SC6, SC7
        dtoverlay=sc16is752-i2c,int_pin=23,addr=0x48
        #RS232 3&4 SC4, SC5
        dtoverlay=sc16is752-i2c,int_pin=24,addr=0x4C
        ##the last two is for the 8 RS232 version
        #RS232 5&6 SC2 SC3
        dtoverlay=sc16is752-i2c,int_pin=25,addr=0x49
        #RS232 7&8 SC0 SC1
        dtoverlay=sc16is752-i2c,int_pin=22,addr=0x4D
        ```
    - reboot the PI ```sudo reboot```
- After rebooting you can check `ls/dev` to see if you can see `ttySC0`, `ttySC1`, `ttySC2`, `ttySC3`.
    - ttySC0 is J8
    - ttySC1 is J7
    - ttySC2 is J4
    - ttySC3 is J5
    - ttySC4 is J9
    - ttySC5 is J10
    - ttySC6 is J14
    - ttySC7 is J15

- Testing the port with demo codes (provided by waveshare). **Or you can use minicom**
    - Download the code
    ```
    wget http://www.waveshare.com/w/upload/b/ba/Serial_Expansion_HAT_code.tar.gz
    tar zxvf Serial_Expansion_HAT_code.tar.gz
    sudo chmod 777 -R Serial_Expansion_HAT_code
    cd Serial_Expansion_HAT_code
    ```
    - test the code
    ```
    #Send data via Serial A
    cd c/uart/send
    make clean 
    make
    sudo ./uart_send
    ```
    ```
    #Receive data via Serial B
    cd c/uart/receive/
    make clean 
    make
    sudo ./uart_receive
    ```

## Test Xsens MTI-630
- On our Pi Hat (SBC_Hat_ Rise), we have a connector that allows us to directly interface with a MTI-630 AHRS. We have a [MTI ROS driver](https://github.com/GSO-soslab/xsens_mti_ros_driver/tree/7aa46b7f0a0576609062aaf46c518940e5fb4853) available for testing the communication and the board setup. The driver is a slightly modified version of the original MTI ROS driver.
- Port: `/dev/ttyS0` or `/dev/ttyAMA0`
- Default UART baudrate: `115200`
- Some [special setup](https://askubuntu.com/questions/1254376/enable-uart-communication-on-pi4-ubuntu-20-04) will be needed for Ubuntu 20.04 user since the raspi-config won't be able to enable the uart.
    - Back up the oroginal config.txt and cmdline.txt files 
    ```
    sudo cp -pr /boot/firmware/cmdline.txt /boot/firmware/cmdline.txt-orig
    sudo cp -pr /boot/firmware/config.txt /boot/firmware/config.txt-orig
    ```
    - Edit `/boot/firmware/config.txt` to comment out `enable_uart=1`
    ```
    #enable_uart=1
    cmdline=cmdline.txt
    ```
    - Remove the console setting `console=serial0,115200` from `/boot/firmware/cmdline.txt`
    - Disable serial service which used the miniUART
    ```
    sudo systemctl stop serial-getty@ttyS0.service
    sudo systemctl disable serial-getty@ttyS0.service
    sudo systemctl mask serial-getty@ttyS0.service
    ```
    - Add user to tty and dialout
    ```
    sudo adduser ${USER} tty
    sudo adduser ${USER} dialout
    ```
    - Reboot your pi
    - Someone also suggested to create a new file `/etc/udev/rules.d/10-local.rules`
    ```
    KERNEL=="ttyS0", SYMLINK+="serial0" GROUP="tty" MODE="0660"
    KERNEL=="ttyAMA0", SYMLINK+="serial1" GROUP="tty" MODE="0660"
    ```
    - Then, reload the udev rules: `sudo udevadm control --reload-rules && sudo udevadm trigger`
    - Add a newline `dtoverlay=disable-bt` to `/boot/firmware/config.txt` underneath `cmdline=cmdline.txt`
    - Worst case scenario, you can mount Xsense upside down and use a UART to USB bridge. This is the easiest fix.
- Disbale the u-boot interface with UART, check [reference](https://askubuntu.com/a/1287847)
    - Install the dependencies on your laptop for building new u-boot
    ```
    sudo apt install git make gcc gcc-aarch64-linux-gnu bison flex
    ```
    - Clone offical u-boot repository
    ```sh
    git clone --depth 1 git://git.denx.de/u-boot.git
    cd u-boot
    ```
    - Modify the *u-boot/configs/rpi_4_defconfig* by adding following lines in the end:
    ```
    CONFIG_BOOTDELAY=-2
    CONFIG_SILENT_CONSOLE=y
    CONFIG_SYS_DEVICE_NULLDEV=y
    CONFIG_SILENT_CONSOLE_UPDATE_ON_SET=y
    CONFIG_SILENT_U_BOOT_ONLY=y
    ```
    - Modify the *u-boot/include/configs/rpi.h* by adding following lines before `#endif`:
    ```c++
    #define CONFIG_EXTRA_ENV_SETTINGS \
    "dhcpuboot=usb start; dhcp u-boot.uimg; bootm\0" \
    "silent=1\0" \
    ENV_DEVICE_SETTINGS \
    ENV_DFU_SETTINGS \
    ENV_MEM_LAYOUT_SETTINGS \
    BOOTENV
    ```
    - Cross compile u-boot for Pi
    ```sh
    cd ~/path/u-boot
    make rpi_4_defconfig
    make CROSS_COMPILE=aarch64-linux-gnu-
    ```
    - Replace the kernal
        - rename the built *u-boot/u-boot.bin* to *uboot_rpi_4.bin*
        - backup the original file in your Pi such as */boot/firmware/uboot_rpi_4.bin.bak*
        - put the built file in your Pi inside */boot/firmware* folder

## Test ADC chip

## Follow the [instruction](http://wiki.ros.org/noetic/Installation/Ubuntu) to install ROS Noetic.
- You can install the base version
- the base version will take about 1 GB space

## Test Bar30 sensor from Blue Robotics
- Download the python testing code from Blue robotics [here](https://github.com/bluerobotics/ms5837-python)
- Install the library `pip install smbus2`

## GPIO control
On the hat we have 5 GPIOs (7,8, 9, 12, 13).
We use the GPIO as output pins to control MOSFET and power supplies to control sensor payloads.
GPIO9, 12, 13 can be configured as normal GPIO.

- First, you need to export the GPIO
```
echo 9 > /sys/class/gpio/export

```
- Second, you can set the direction of the GPIO
```
echo out > /sys/class/gpio/direction
```

- Finally, you can set the GPIO to High[1] or Low [0]
```
echo 1 > /sys/class/gpio/direction
```
***Note***: For GPIO7 and GPIO8, they are originally used as chip select pin for SPI in the PI system. To free them to become a regular GPIO, you need to add the following line in `/boot/config.txt` and `/boot/firmware/config.txt` file after the line `dtparam=spi=off`. The added line will remapp the chip select pin to other GPIOs, i.e., 20 and 21 here.
Then, you can reboot the PI, and `GPIO7` and `GPIO8` can be used as normal GPIOs.
```
dtoverlay=spi0-cs,cs0_pin=20,cs1_pin=21
```

## Remote setup
The ubuntu we are using is server, to change the hostname, please refere to `/etc/cloud/templates/hosts.debian.tmpl`

## Make new image for Pi:
[reference](https://raspberrytips.com/create-image-sd-card/)
Notes: our image is available on request: please contact mzhou@uri.edu for more information.
- On Ubuntu:
    - check the Pi SDcard on ubuntu through the SD card reader:
    ```sh
    sudo fdisk -l
    ```
    - make new image based your system
    ```sh
    sudo dd bs=4M status=progress if=[device name] of=[image name]
    # Example
    # sudo dd bs=4M status=progress if=/dev/sde of=/your-path/vehicle-name_day_month_year.img
    ```
    - shrink image on Ubuntu:
    ```sh
    # dependency
    sudo apt-get install gparted
    # get shrink script
    wget https://raw.githubusercontent.com/GSO-soslab/PiShrink/master/pishrink.sh
    chmod +x pishrink.sh
    sudo mv pishrink.sh /usr/local/bin
    # usage
    cd /your-path
    cp your_file.img your_file_backup.img
    sudo pishrink.sh your_file.img
    ```
- On Windows: check the reference
- Verify:
    - check ADC: individually Bring up the Power Minotor in the `bringup_test.launch`
    - check AHRS: individually Bring up Xsens AHRS in the `bringup_test.launch`
    - check Pico: individually Bring up Pico MCU in the `bringup_test.launch`

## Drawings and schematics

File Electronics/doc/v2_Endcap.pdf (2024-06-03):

## ALPHA Race

## ALPHA

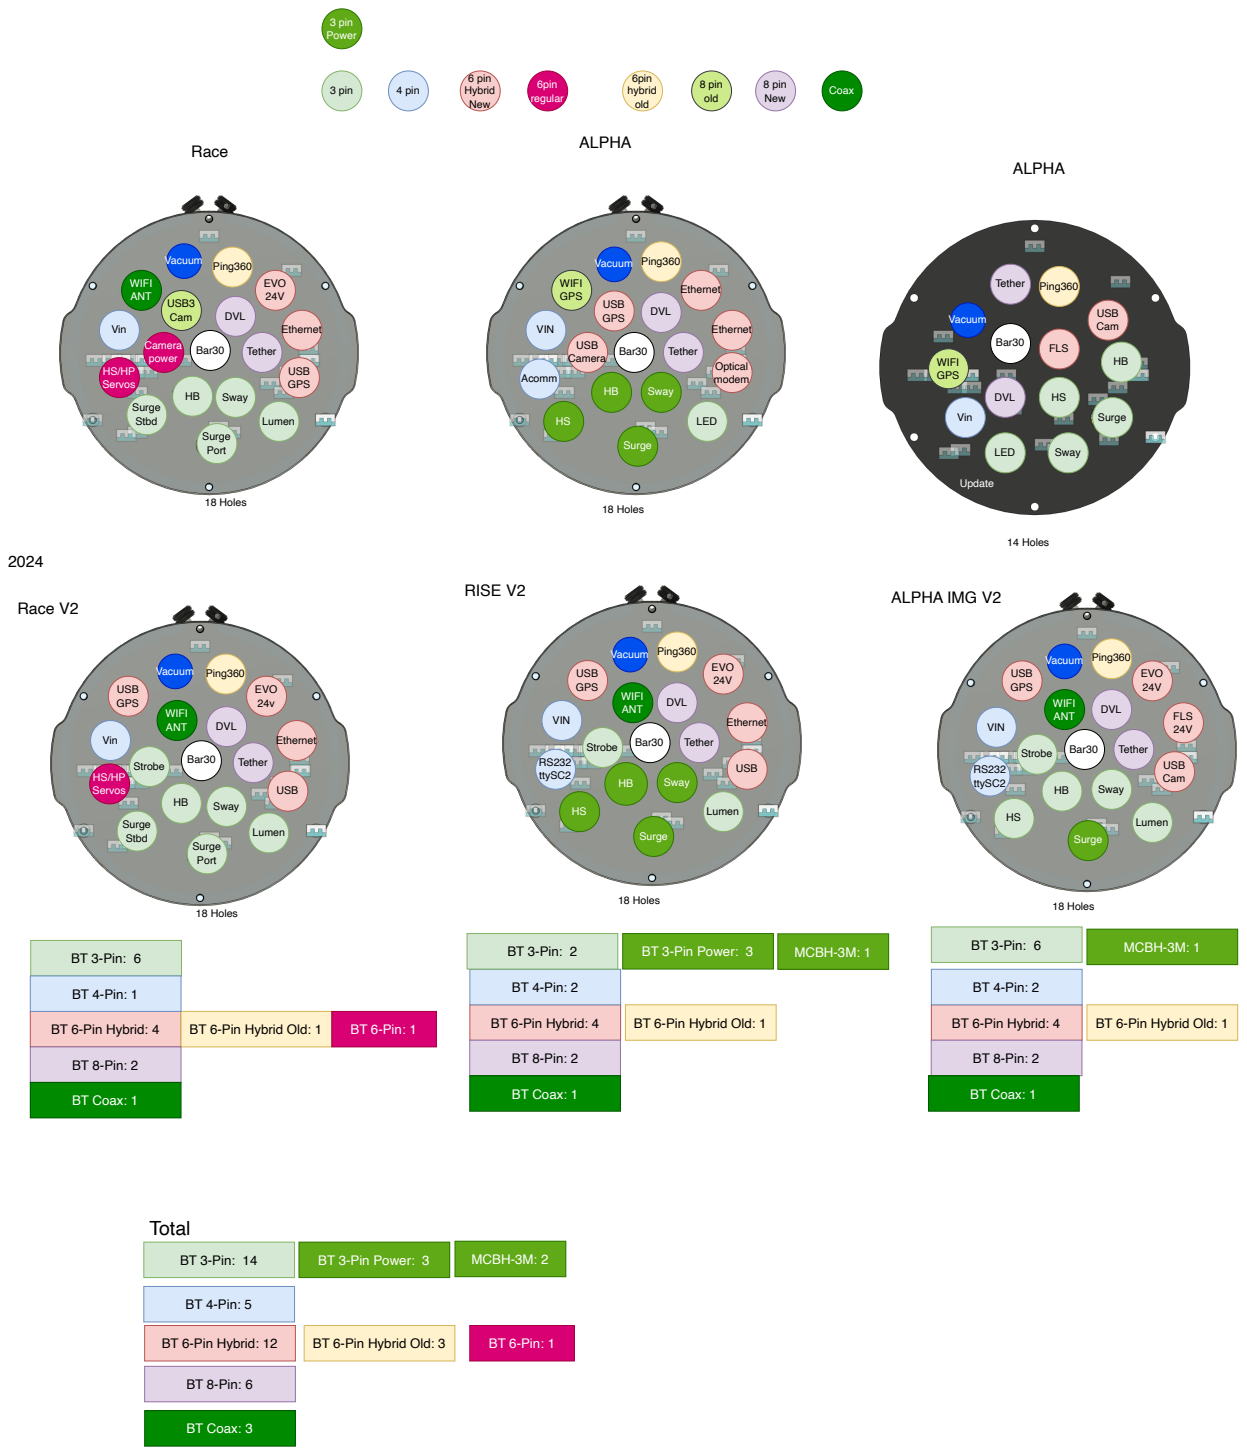
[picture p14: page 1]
3 pin; 4 pin; 6 pin Hybrid New; 6pin hybrid old; 8 pin old; 8 pin New; USB3 Cam; Surge Stbd; Surge Port; Bar30; Vacuum; DVL; EVO 24V; Lumen; 18 Holes; 14 Holes; VIN; Acomm; Ethernet; LED; Sway; Surge; Optical modem; USB Camera; Ping360; WIFI GPS; Tether; Vin; FLS; 6pin regular; Camera power; USB Cam; USB GPS; RS232 ttySC2; Strobe; RISE V2; USB; Coax; WIFI ANT; Update; FLS 24V; ALPHA IMG V2; 3 pin Power; Race V2; EVO 24v; HS/HP Servos; BT 3-Pin: 6; BT 8-Pin: 2; BT 4-Pin: 1; BT Coax: 1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

BT 3-Pin Power: 3

BT 6-Pin Hybrid: 4 | BT 6-Pin Hybrid Old: 1 | BT 6-Pin: 1

BT 8-Pin: 2 | BT 8-Pin: 2

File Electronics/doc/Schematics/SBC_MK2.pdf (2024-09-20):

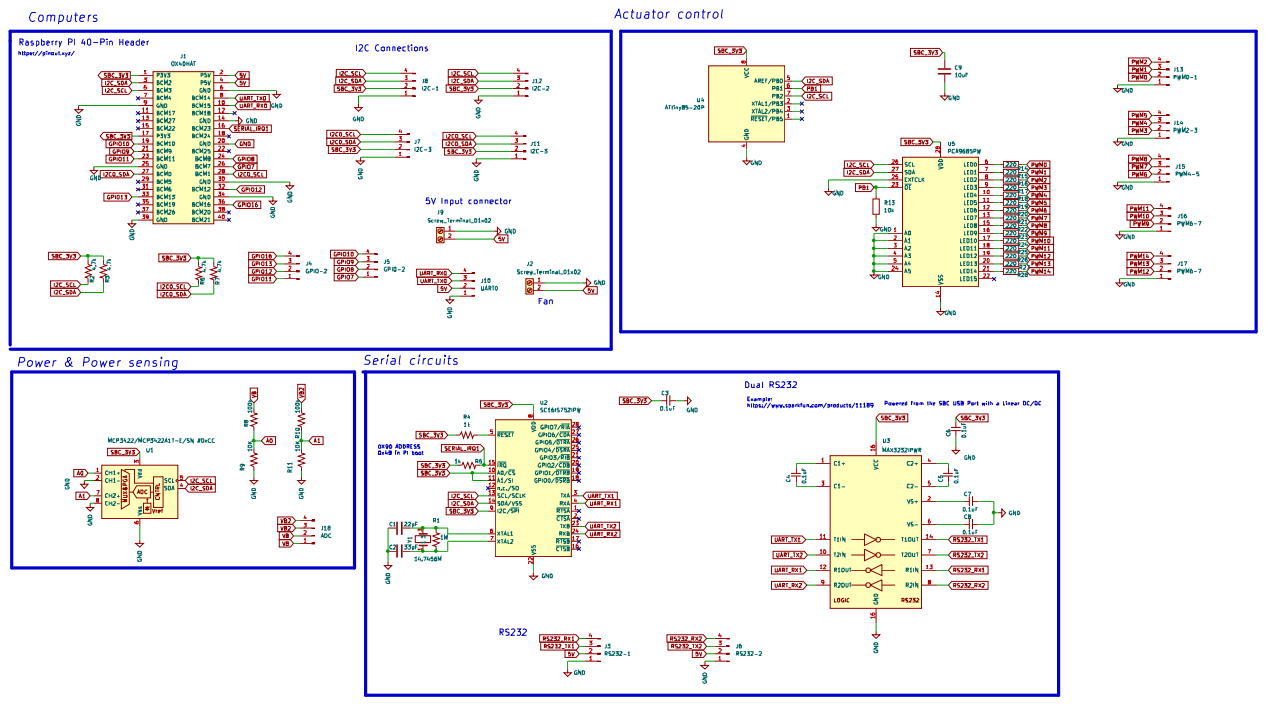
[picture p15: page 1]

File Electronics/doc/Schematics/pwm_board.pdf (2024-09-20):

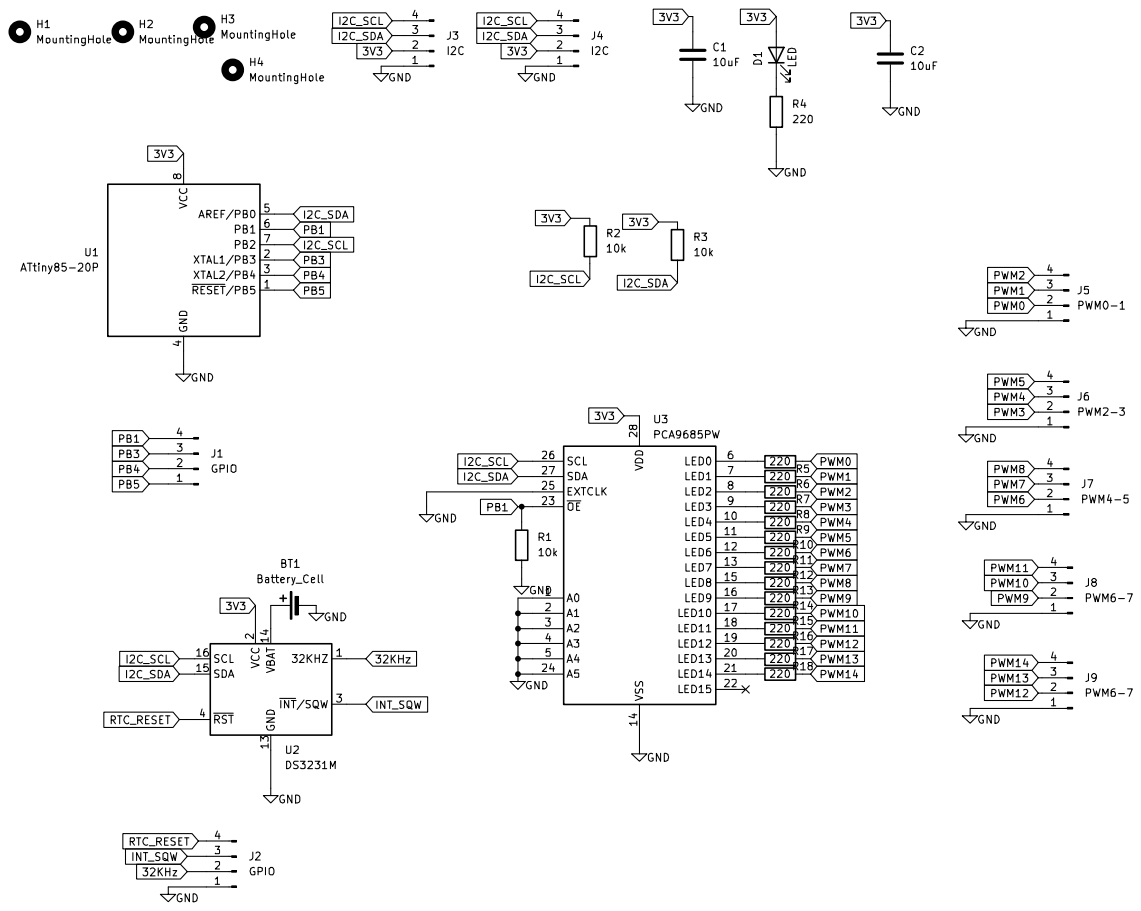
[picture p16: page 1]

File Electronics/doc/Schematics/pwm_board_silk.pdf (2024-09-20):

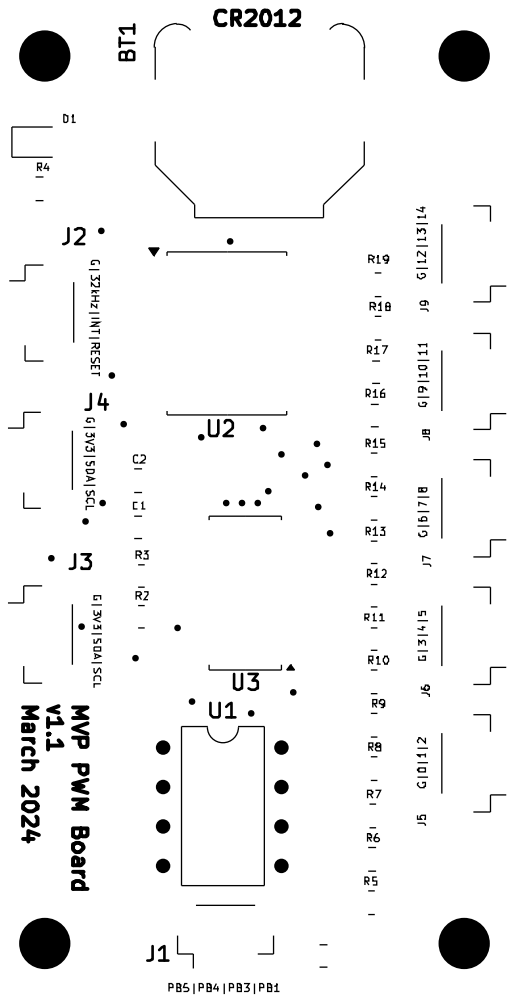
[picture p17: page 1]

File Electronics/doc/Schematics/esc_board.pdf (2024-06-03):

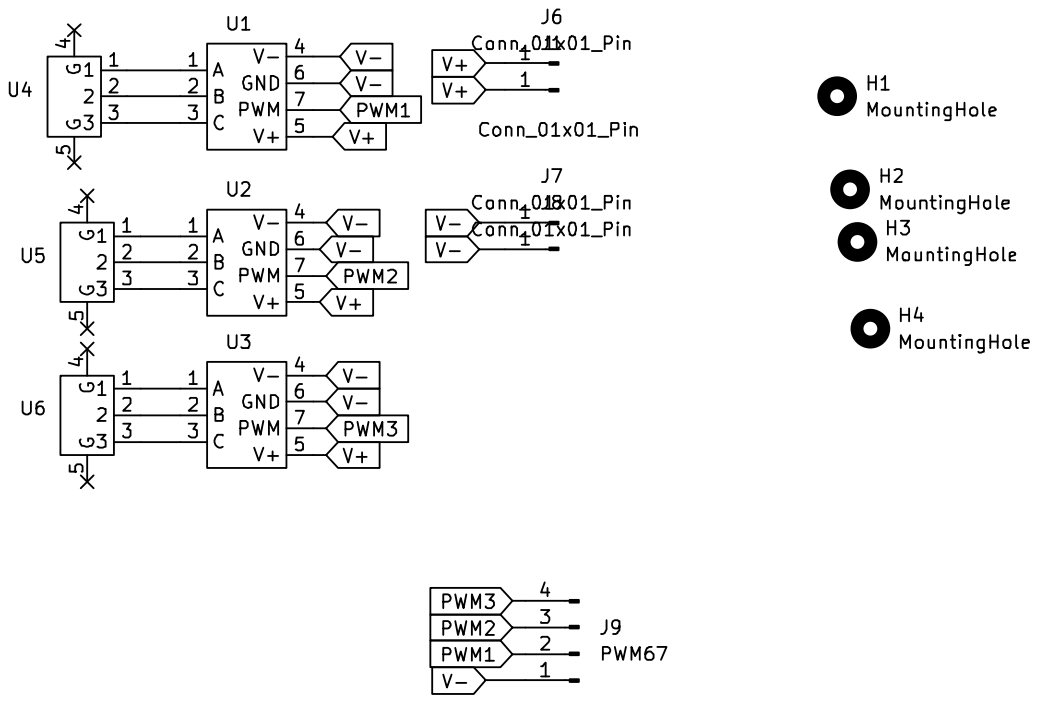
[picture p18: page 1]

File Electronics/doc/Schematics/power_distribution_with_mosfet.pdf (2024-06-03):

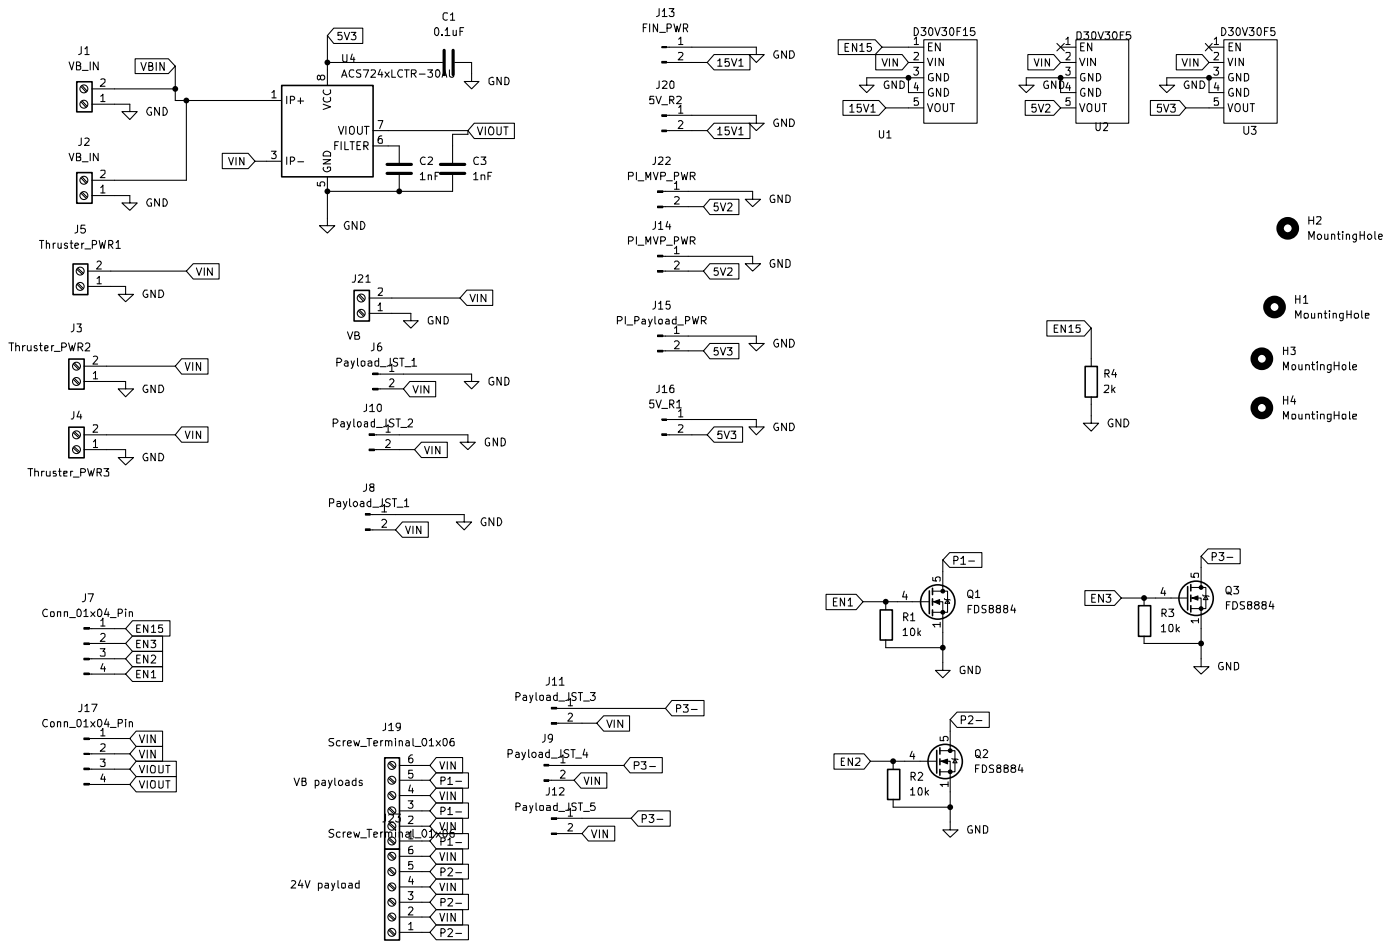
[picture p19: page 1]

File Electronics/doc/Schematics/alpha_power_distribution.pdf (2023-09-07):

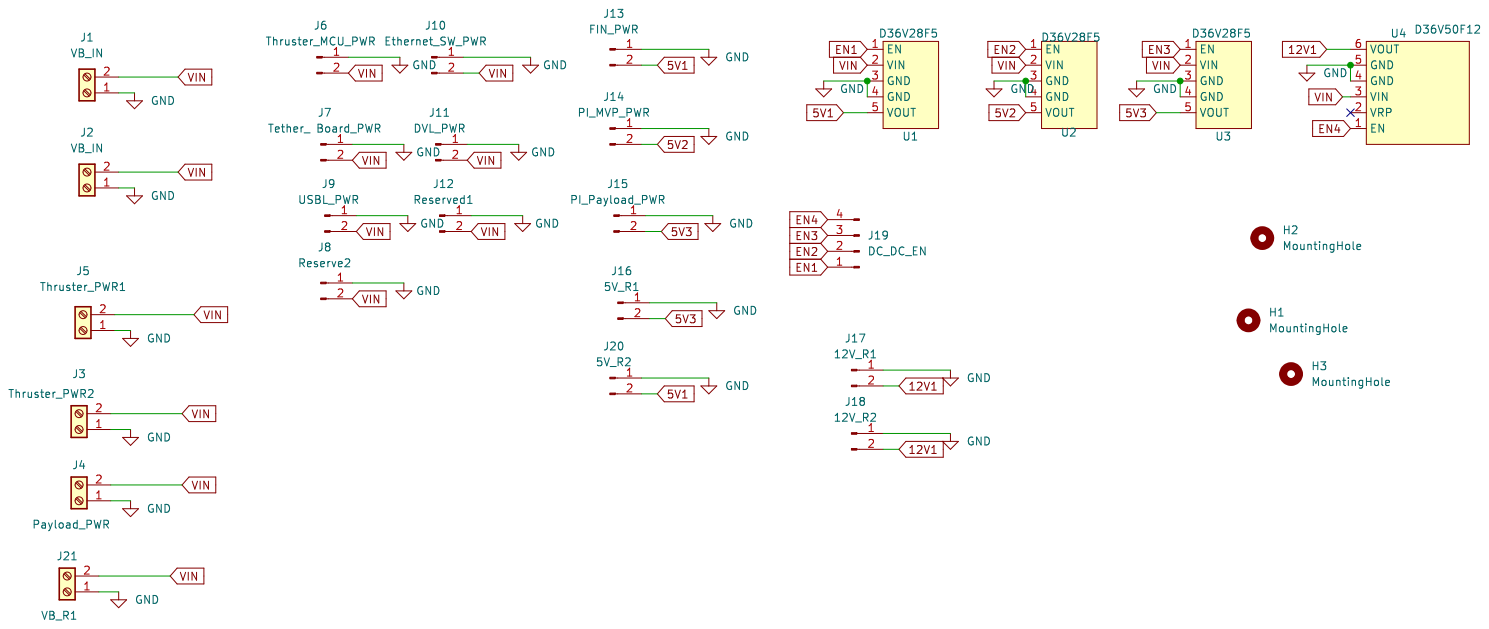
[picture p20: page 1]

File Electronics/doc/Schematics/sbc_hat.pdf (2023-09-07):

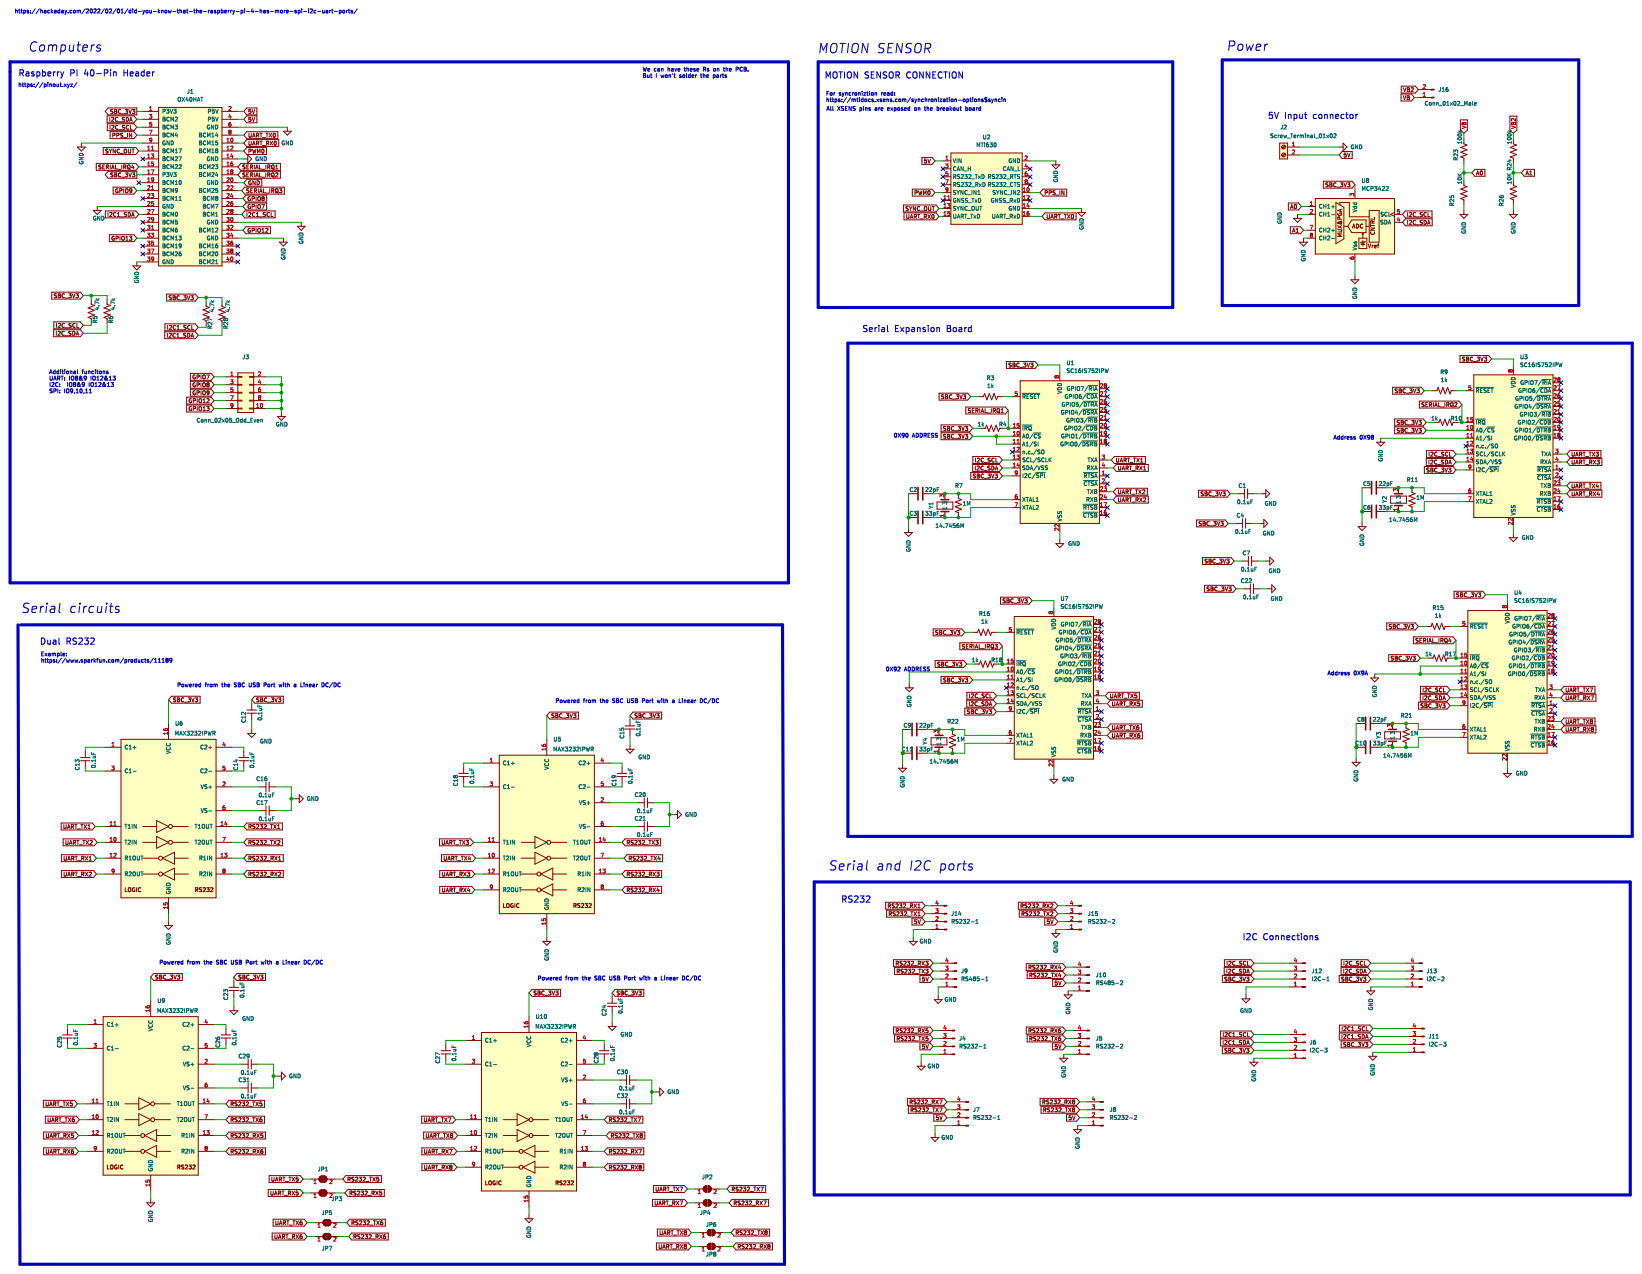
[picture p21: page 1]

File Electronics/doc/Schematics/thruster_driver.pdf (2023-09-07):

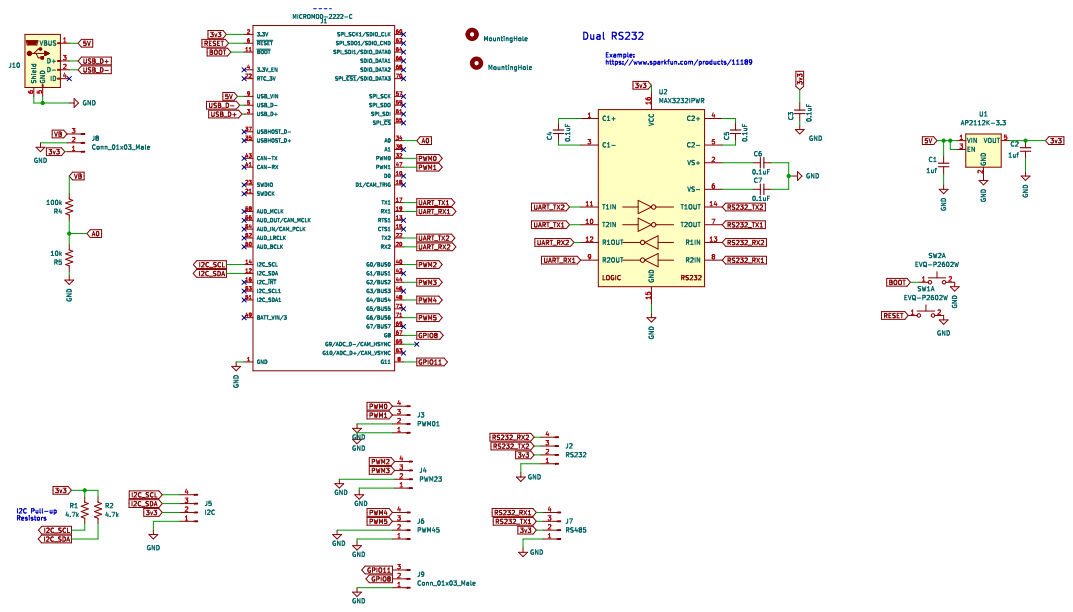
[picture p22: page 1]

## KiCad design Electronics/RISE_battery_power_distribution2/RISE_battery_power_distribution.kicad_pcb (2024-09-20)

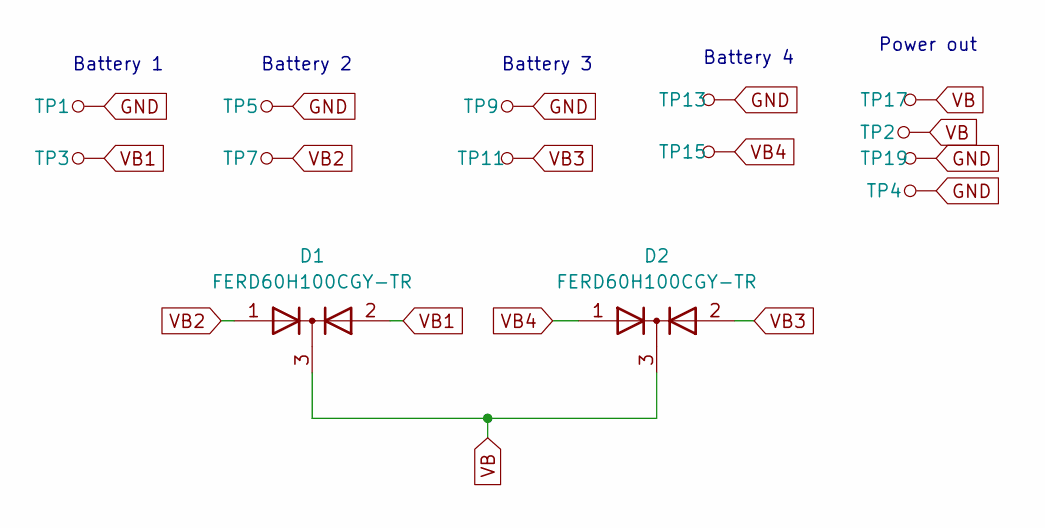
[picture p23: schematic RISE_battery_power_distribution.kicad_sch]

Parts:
D1, D2: FERD60H100CGY-TR; STPS41L60CG-TR
TP1, TP2, TP3, TP4, TP5, TP7, TP9, TP11, TP13, TP15, TP17, TP19: 5016; Test_Point_3.43x1.78mm; MPN 5016; Digi-Key_PN 36-5016CT-ND

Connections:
GND: TP1.1, TP4.1, TP5.1, TP9.1, TP13.1, TP19.1
VB: D1.3 (K), D2.3 (K), TP2.1, TP17.1
VB1: D1.2 (A), TP3.1
VB2: D1.1 (A), TP7.1
VB3: D2.2 (A), TP11.1
VB4: D2.1 (A), TP15.1

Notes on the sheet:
Battery 3
Battery 2
Battery 1
Battery 4
Power out

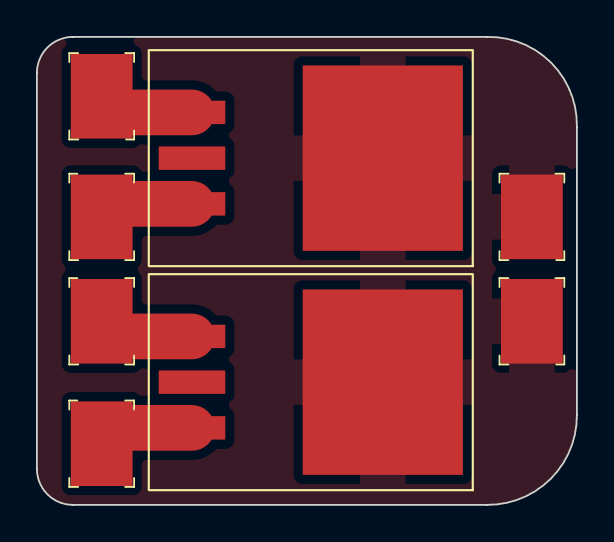
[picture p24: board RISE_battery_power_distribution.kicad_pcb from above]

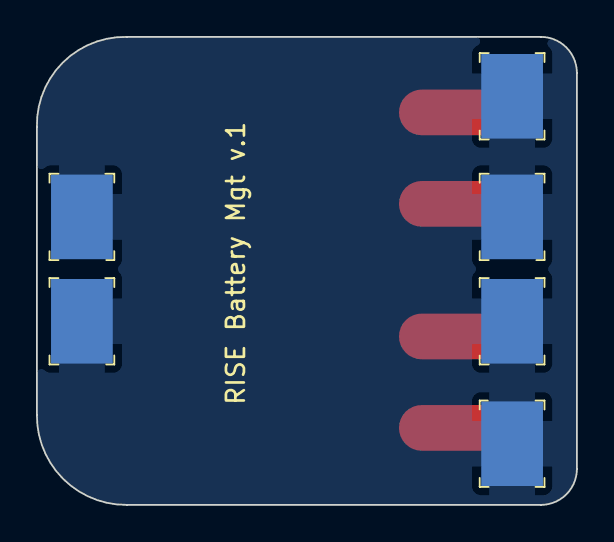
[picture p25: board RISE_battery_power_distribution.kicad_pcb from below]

Board: 2 copper layers, 30.0 x 26.0 mm, 14 parts (6 on the bottom side), 6 nets.

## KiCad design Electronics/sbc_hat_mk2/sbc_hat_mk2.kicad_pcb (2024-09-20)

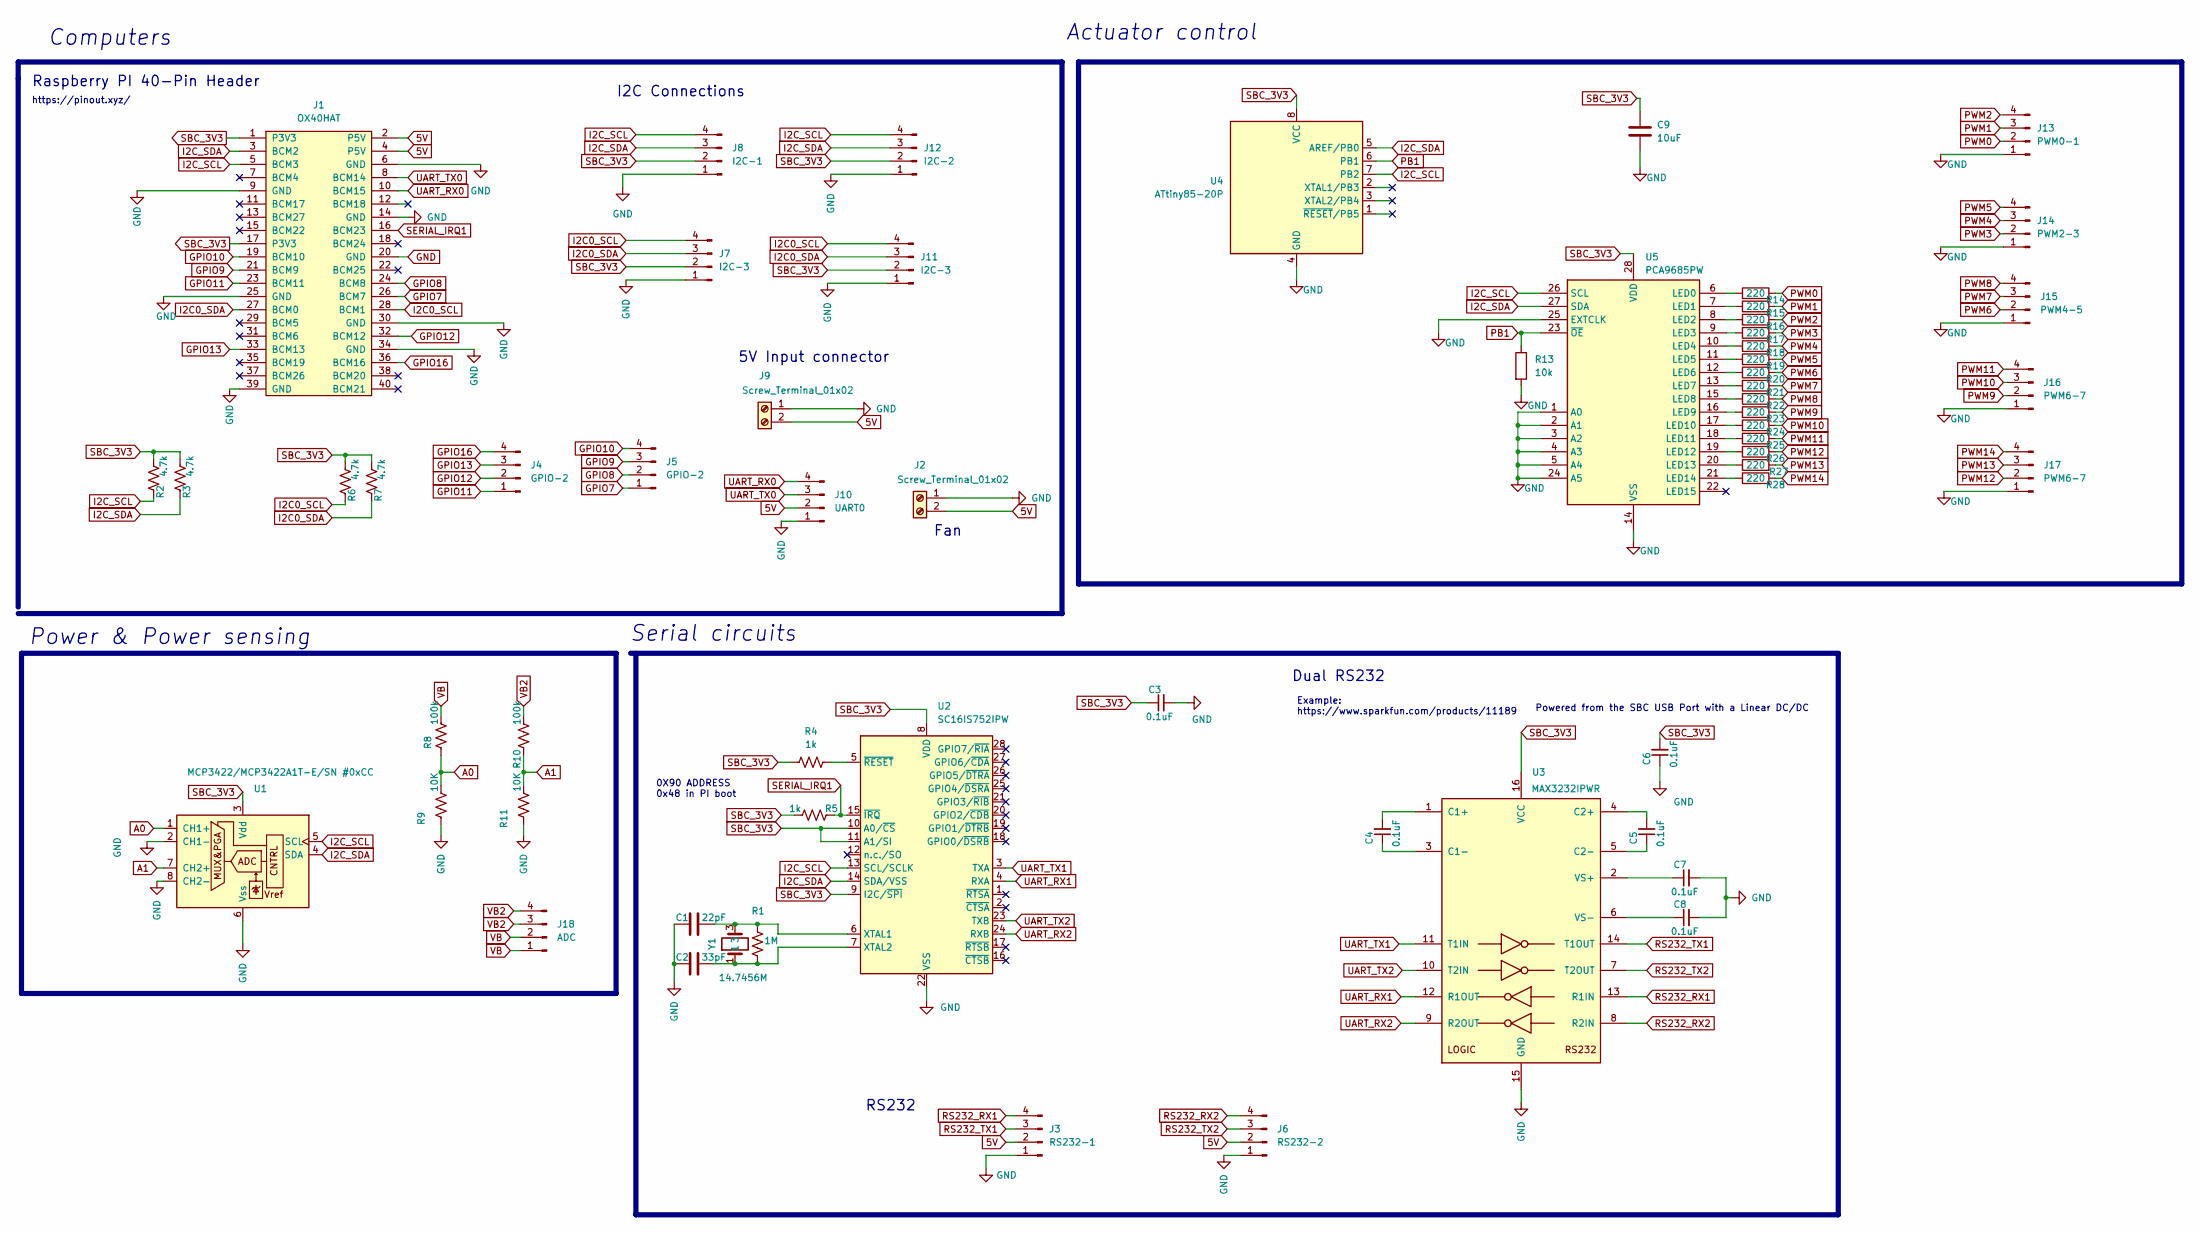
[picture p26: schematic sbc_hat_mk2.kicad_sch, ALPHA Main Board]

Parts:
C1: 22pF; C_0805_2012Metric; Manufacturer_Part_Number 08055J220FBTTR; Digikey Part Number 478-11911-1-ND
C2: 33pF; C_0805_2012Metric; Manufacturer_Part_Number 600F330FT250XT; Digikey Part Number 1284-1049-1-ND
C3, C4, C5, C6, C7, C8: 0.1uF; C_0805_2012Metric; Manufacturer_Part_Number 0805ZC104JAT2A; Digikey Part Number 478-11627-1-ND
C9: 10uF; C_0805_2012Metric
J1: OX40HAT; PinSocket_2x20_P2.54mm_Vertical; Mouser Part Number 474-PRT-14017
J2, J9: Screw_Terminal_01x02; TerminalBlock_Phoenix_MPT-0,5-2-2.54_1x02_P2.54mm_Horizontal; Manufacturer_Part_Number 1725656; Mouser Part Number 651-1725656
J3: RS232-1; JST_SH_BM04B-SRSS-TB_1x04-1MP_P1.00mm_Vertical; Manufacturer_Part_Number 4328; Digikey Part Number 1528-4328-ND
J4, J5: GPIO-2; JST_SH_BM04B-SRSS-TB_1x04-1MP_P1.00mm_Vertical; Manufacturer_Part_Number 4328; Digikey Part Number 1528-4328-ND
J6: RS232-2; JST_SH_BM04B-SRSS-TB_1x04-1MP_P1.00mm_Vertical; Manufacturer_Part_Number 4328; Digikey Part Number 1528-4328-ND
J7, J11: I2C-3; JST_SH_BM04B-SRSS-TB_1x04-1MP_P1.00mm_Vertical; Manufacturer_Part_Number 4328; Digikey Part Number 1528-4328-ND
J8: I2C-1; JST_SH_BM04B-SRSS-TB_1x04-1MP_P1.00mm_Vertical; Manufacturer_Part_Number 4328; Digikey Part Number 1528-4328-ND
J10: UART0; JST_SH_BM04B-SRSS-TB_1x04-1MP_P1.00mm_Vertical; Manufacturer_Part_Number 4328; Digikey Part Number 1528-4328-ND
J12: I2C-2; JST_SH_BM04B-SRSS-TB_1x04-1MP_P1.00mm_Vertical; Manufacturer_Part_Number 4328; Digikey Part Number 1528-4328-ND
J13: PWM0-1; JST_SH_BM04B-SRSS-TB_1x04-1MP_P1.00mm_Vertical; Manufacturer_Part_Number 4328; Digikey Part Number 1528-4328-ND
J14: PWM2-3; JST_SH_BM04B-SRSS-TB_1x04-1MP_P1.00mm_Vertical; Manufacturer_Part_Number 4328; Digikey Part Number 1528-4328-ND
J15: PWM4-5; JST_SH_BM04B-SRSS-TB_1x04-1MP_P1.00mm_Vertical; Manufacturer_Part_Number 4328; Digikey Part Number 1528-4328-ND
J16, J17: PWM6-7; JST_SH_BM04B-SRSS-TB_1x04-1MP_P1.00mm_Vertical; Manufacturer_Part_Number 4328; Digikey Part Number 1528-4328-ND
J18: ADC; JST_SH_BM04B-SRSS-TB_1x04-1MP_P1.00mm_Vertical; Manufacturer_Part_Number 4328; Digikey Part Number 1528-4328-ND
R1: 1M; R_0805_2012Metric; Manufacturer_Part_Number ERA-6AED105V; Mouser Part Number 667-ERA-6AED105V
R2, R3, R6, R7: 4.7k; R_0805_2012Metric; Manufacturer_Part_Number ERJ-T06J472V; Mouser Part Number 667-ERJ-T06J472V
R4, R5: 1k; R_0805_2012Metric; Manufacturer_Part_Number 1-2176092-8; Digikey Part Number A110543CT-ND
R8, R10: 100k; R_0805_2012Metric; Manufacturer_Part_Number ERA-6AEB104V; Mouser Part Number 667-ERA-6AEB104V
R9, R11: 10K; R_0805_2012Metric; Manufacturer_Part_Number ERA-6AEB104V; Mouser Part Number 667-ERA-6AEB104V
R13: 10k; R_0805_2012Metric
R14, R15, R16, R17, R18, R19, R20, R21, R22, R23, R24, R25, R26, R27, R28: 220; R_0805_2012Metric
U1: MCP3422/MCP3422A1T-E/SN #0xCC; SOIC-8-1EP_3.9x4.9mm_P1.27mm_EP2.29x3mm
U2: SC16IS752IPW; TSSOP-28_4.4x9.7mm_P0.65mm
U3: MAX3232IPWR; TSSOP-16_4.4x5mm_P0.65mm; Manufacturer_Part_Number MAX3232IPWR; Mouser Part Number 595-MAX3232IPWR
U4: ATtiny85-20P; DIP-8_W7.62mm
U5: PCA9685PW; TSSOP-28_4.4x9.7mm_P0.65mm
Y1: 14.7456M; Crystal_SMD_3225-4Pin_3.2x2.5mm

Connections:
5V: J1.2 (P5V), J1.4 (P5V), J2.2, J3.2, J6.2, J9.2, J10.2
A0: R8.2, R9.1, U1.1 (CH1+)
A1: R10.2, R11.1, U1.7 (CH2+)
GND: C1.1, C2.1, C3.2, C6.1, C7.2, C8.2, C9.2, J1.6 (GND), J1.9 (GND), J1.14 (GND), J1.20 (GND), J1.25 (GND), J1.30 (GND), J1.34 (GND), J1.39 (GND), J2.1, J3.1, J6.1, J7.1, J8.1, J9.1, J10.1, J11.1, J12.1, J13.1, J14.1, J15.1, J16.1, J17.1, R9.2, R11.2, R13.2, U1.2 (CH1-), U1.6 (Vss), U1.8 (CH2-), U2.22 (VSS), U3.15 (GND), U4.4 (GND), U5.1 (A0), U5.2 (A1), U5.3 (A2), U5.4 (A3), U5.5 (A4), U5.14 (VSS), U5.24 (A5), U5.25 (EXTCLK)
GPIO7: J1.26 (BCM7), J5.1
GPIO8: J1.24 (BCM8), J5.2
GPIO9: J1.21 (BCM9), J5.3
GPIO10: J1.19 (BCM10), J5.4
GPIO11: J1.23 (BCM11), J4.1
GPIO12: J1.32 (BCM12), J4.2
GPIO13: J1.33 (BCM13), J4.3
GPIO16: J1.36 (BCM16), J4.4
I2C0_SCL: J1.28 (BCM1), J7.4, J11.4, R6.1
I2C0_SDA: J1.27 (BCM0), J7.3, J11.3, R7.1
I2C_SCL: J1.5 (BCM3), J8.4, J12.4, R2.1, U1.5 (SCL), U2.13 (SCL/SCLK), U4.7 (PB2), U5.26 (SCL)
I2C_SDA: J1.3 (BCM2), J8.3, J12.3, R3.1, U1.4 (SDA), U2.14 (SDA/VSS), U4.5 (AREF/PB0), U5.27 (SDA)
unnamed: C1.2, R1.1, U2.6 (XTAL1), Y1.3
unnamed: C2.2, R1.2, U2.7 (XTAL2), Y1.1
unnamed: R4.2, U2.5 (~RESET)
unnamed: C4.2, U3.1 (C1+)
unnamed: C4.1, U3.3 (C1-)
unnamed: C5.2, U3.4 (C2+)
unnamed: C5.1, U3.5 (C2-)
unnamed: C7.1, U3.2 (VS+)
unnamed: C8.1, U3.6 (VS-)
unnamed: R14.1, U5.6 (LED0)
unnamed: R15.1, U5.7 (LED1)
unnamed: R16.1, U5.8 (LED2)
unnamed: R17.1, U5.9 (LED3)
unnamed: R18.1, U5.10 (LED4)
unnamed: R19.1, U5.11 (LED5)
unnamed: R20.1, U5.12 (LED6)
unnamed: R21.1, U5.13 (LED7)
unnamed: R22.1, U5.15 (LED8)
unnamed: R23.1, U5.16 (LED9)
unnamed: R24.1, U5.17 (LED10)
unnamed: R25.1, U5.18 (LED11)
unnamed: R26.1, U5.19 (LED12)
unnamed: R27.1, U5.20 (LED13)
unnamed: R28.1, U5.21 (LED14)
PB1: R13.1, U4.6 (PB1), U5.23 (~OE)
PWM0: J13.2, R14.2
PWM1: J13.3, R15.2
PWM2: J13.4, R16.2
PWM3: J14.2, R17.2
PWM4: J14.3, R18.2
PWM5: J14.4, R19.2
PWM6: J15.2, R20.2
PWM7: J15.3, R21.2
PWM8: J15.4, R22.2
PWM9: J16.2, R23.2
PWM10: J16.3, R24.2
PWM11: J16.4, R25.2
PWM12: J17.2, R26.2
PWM13: J17.3, R27.2
PWM14: J17.4, R28.2
RS232_RX1: J3.4, U3.13 (R1IN)
RS232_RX2: J6.4, U3.8 (R2IN)
RS232_TX1: J3.3, U3.14 (T1OUT)
RS232_TX2: J6.3, U3.7 (T2OUT)
SBC_3V3: C3.1, C6.2, C9.1, J1.1 (P3V3), J1.17 (P3V3), J7.2, J8.2, J11.2, J12.2, R2.2, R3.2, R4.1, R5.2, R6.2, R7.2, U1.3 (Vdd), U2.8 (VDD), U2.9 (I2C/~SPI), U2.10 (A0/~CS), U2.11 (A1/SI), U3.16 (VCC), U4.8 (VCC), U5.28 (VDD)
SERIAL_IRQ1: J1.16 (BCM23), R5.1, U2.15 (~IRQ)
UART_RX0: J1.10 (BCM15), J10.4
UART_RX1: U2.4 (RXA), U3.12 (R1OUT)
UART_RX2: U2.24 (RXB), U3.9 (R2OUT)
UART_TX0: J1.8 (BCM14), J10.3
UART_TX1: U2.3 (TXA), U3.11 (T1IN)
UART_TX2: U2.23 (TXB), U3.10 (T2IN)
VB: J18.1, J18.2, R8.1
VB2: J18.3, J18.4, R10.1

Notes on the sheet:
I2C Connections
0X90 ADDRESS 0x48 in PI boot
5V Input connector
RS232
Serial circuits
Dual RS232
Power & Power sensing
Example: https://www.sparkfun.com/products/11189
Fan
Computers
https://pinout.xyz/
Actuator control
Raspberry PI 40-Pin Header
Powered from the SBC USB Port with a Linear DC/DC

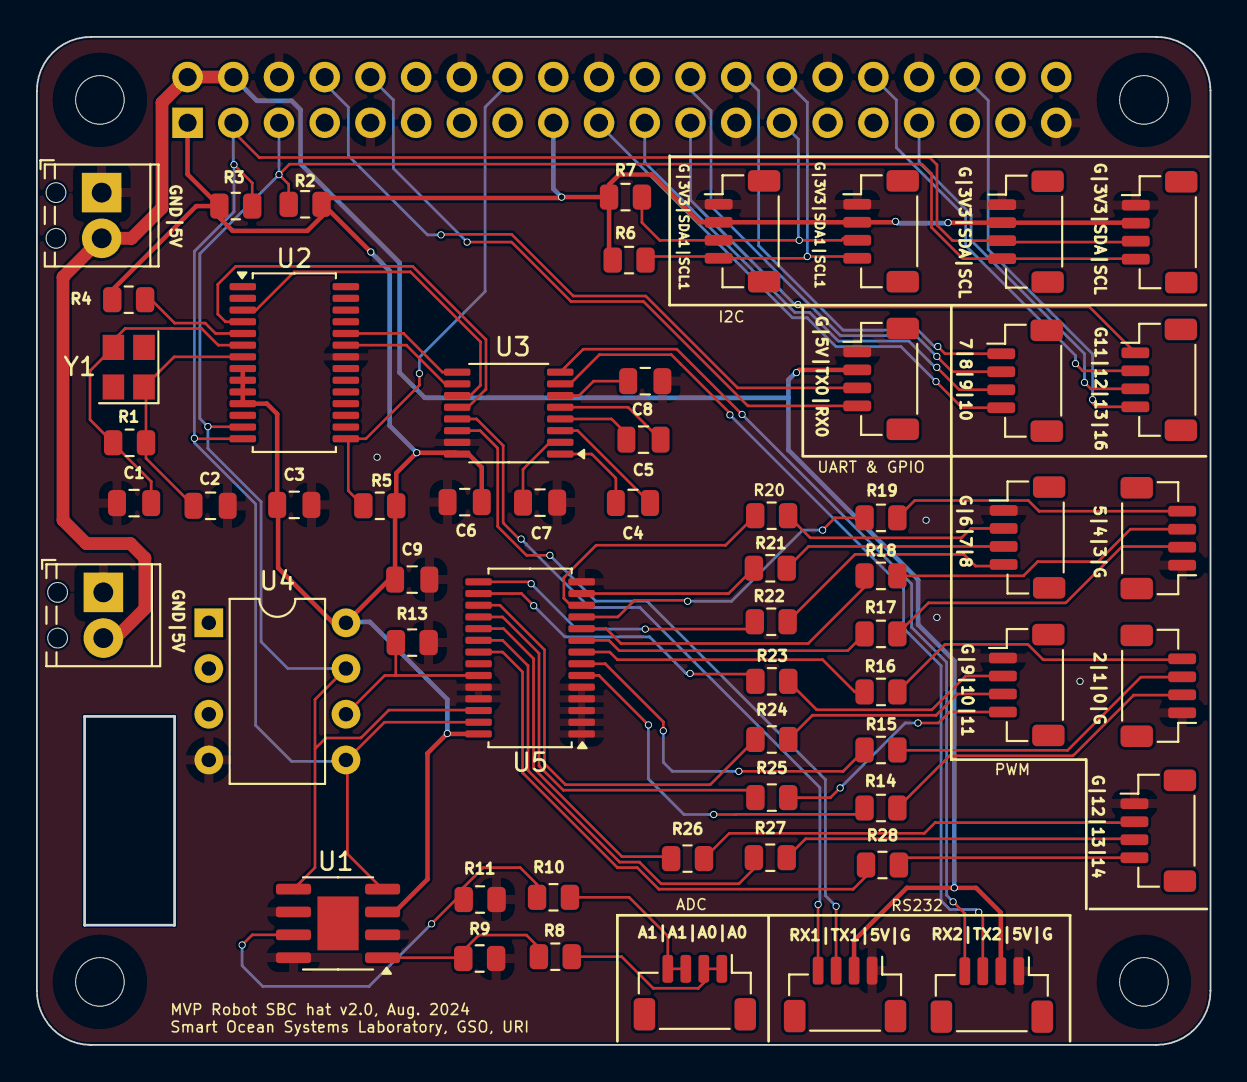
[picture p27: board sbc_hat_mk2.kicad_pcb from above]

Board: 2 copper layers, 65.2 x 56.0 mm, 64 parts (1 on the bottom side), 70 nets.

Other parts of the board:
MH1, MH2, MH3, MH4: MountingHole_2.7mm_M2.5

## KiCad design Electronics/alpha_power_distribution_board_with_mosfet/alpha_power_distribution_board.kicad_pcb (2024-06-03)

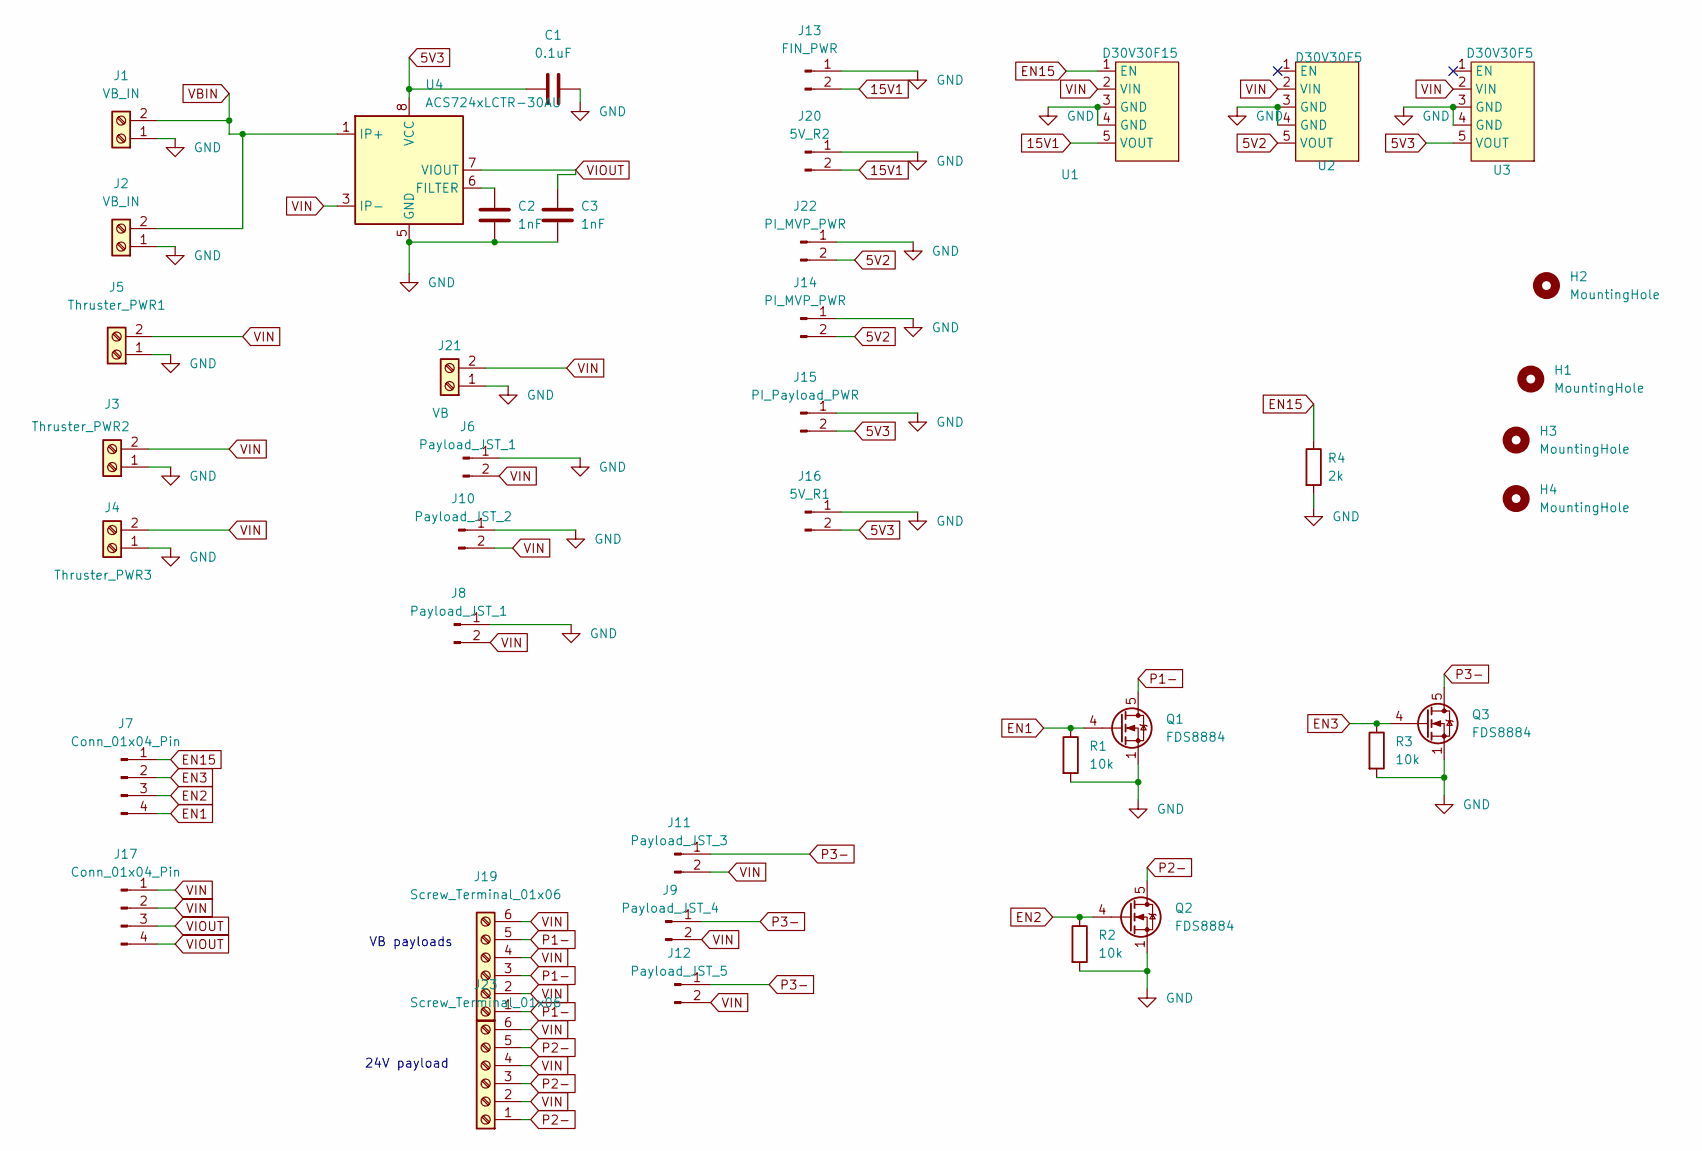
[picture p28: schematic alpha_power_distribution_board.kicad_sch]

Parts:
C1: 0.1uF; C_0805_2012Metric
C2, C3: 1nF; C_0805_2012Metric
H1, H2, H3, H4: MountingHole; MountingHole_2.7mm_M2.5
J1, J2: VB_IN; Pololu_5mm
J3: Thruster_PWR2; Pololu_5mm
J4: Thruster_PWR3; Pololu_5mm
J5: Thruster_PWR1; Pololu_5mm
J6, J8: Payload_JST_1; JST_XH_B2B-XH-A_1x02_P2.50mm_Vertical
J7, J17: Conn_01x04_Pin; JST_SH_BM04B-SRSS-TB_1x04-1MP_P1.00mm_Vertical
J9: Payload_JST_4; JST_XH_B02B-XH-A_02x2.50mm_Straight
J10: Payload_JST_2; JST_XH_B02B-XH-A_02x2.50mm_Straight
J11: Payload_JST_3; JST_XH_B02B-XH-A_02x2.50mm_Straight
J12: Payload_JST_5; JST_XH_B02B-XH-A_02x2.50mm_Straight
J13: FIN_PWR; JST_XH_B02B-XH-A_02x2.50mm_Straight
J14, J22: PI_MVP_PWR; JST_XH_B02B-XH-A_02x2.50mm_Straight
J15: PI_Payload_PWR; JST_XH_B02B-XH-A_02x2.50mm_Straight
J16: 5V_R1; JST_XH_B02B-XH-A_02x2.50mm_Straight
J19, J23: Screw_Terminal_01x06; TerminalBlock_TE_282834-6_1x06_P2.54mm_Horizontal
J20: 5V_R2; JST_XH_B02B-XH-A_02x2.50mm_Straight
J21: VB; Pololu_5mm
Q1, Q2, Q3: FDS8884; SOIC-8_3.9x4.9mm_P1.27mm
R1, R2, R3: 10k; R_0805_2012Metric
R4: 2k; R_0805_2012Metric
U1: D30V30F15; D36V28F5
U2, U3: D30V30F5; D36V28F5
U4: ACS724xLCTR-30AU; SOIC-8_3.9x4.9mm_P1.27mm

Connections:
5V2: J14.2, J22.2, U2.5 (VOUT)
5V3: C1.1, J15.2, J16.2, U3.5 (VOUT), U4.8 (VCC)
15V1: J13.2, J20.2, U1.5 (VOUT)
EN1: J7.4, Q1.4 (G), R1.1
EN2: J7.3, Q2.4 (G), R2.1
EN3: J7.2, Q3.4 (G), R3.1
EN15: J7.1, R4.1, U1.1 (EN)
GND: C1.2, C2.1, C3.1, J1.1, J2.1, J3.1, J4.1, J5.1, J6.1, J8.1, J10.1, J13.1, J14.1, J15.1, J16.1, J20.1, J21.1, J22.1, Q1.1 (S), Q1.2 (S), Q1.3 (S), Q2.1 (S), Q2.2 (S), Q2.3 (S), Q3.1 (S), Q3.2 (S), Q3.3 (S), R1.2, R2.2, R3.2, R4.2, U1.3 (GND), U1.4 (GND), U2.3 (GND), U2.4 (GND), U3.3 (GND), U3.4 (GND), U4.5 (GND)
unnamed: C2.2, U4.6 (FILTER)
P1-: J19.1, J19.3, J19.5, Q1.5 (D), Q1.6 (D), Q1.7 (D), Q1.8 (D)
P2-: J23.1, J23.3, J23.5, Q2.5 (D), Q2.6 (D), Q2.7 (D), Q2.8 (D)
P3-: J9.1, J11.1, J12.1, Q3.5 (D), Q3.6 (D), Q3.7 (D), Q3.8 (D)
VBIN: J1.2, J2.2, U4.1 (IP+), U4.2 (IP+)
VIN: J3.2, J4.2, J5.2, J6.2, J8.2, J9.2, J10.2, J11.2, J12.2, J17.1, J17.2, J19.2, J19.4, J19.6, J21.2, J23.2, J23.4, J23.6, U1.2 (VIN), U2.2 (VIN), U3.2 (VIN), U4.3 (IP-), U4.4 (IP-)
VIOUT: C3.2, J17.3, J17.4, U4.7 (VIOUT)

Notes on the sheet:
VB payloads
24V payload

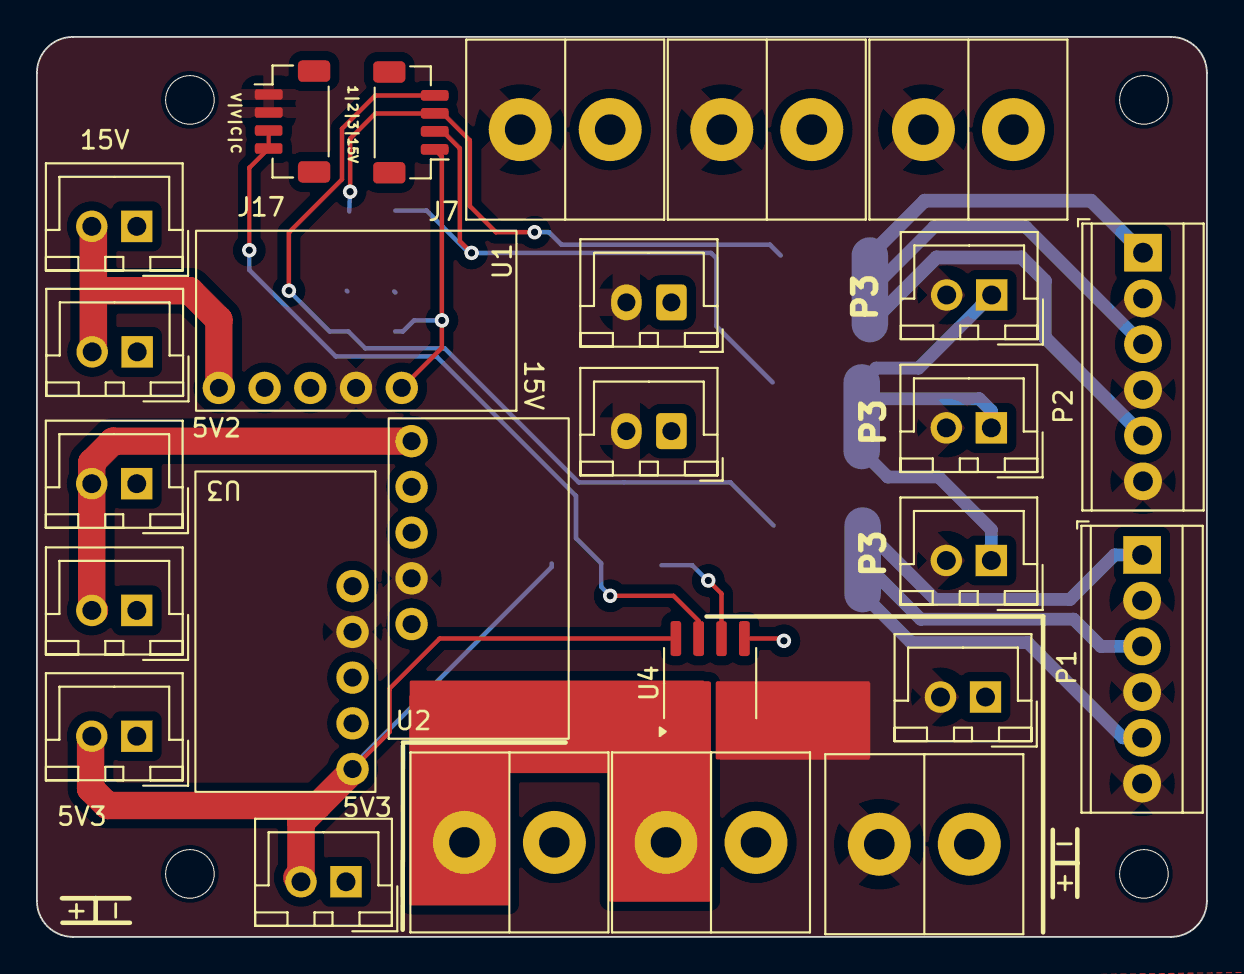
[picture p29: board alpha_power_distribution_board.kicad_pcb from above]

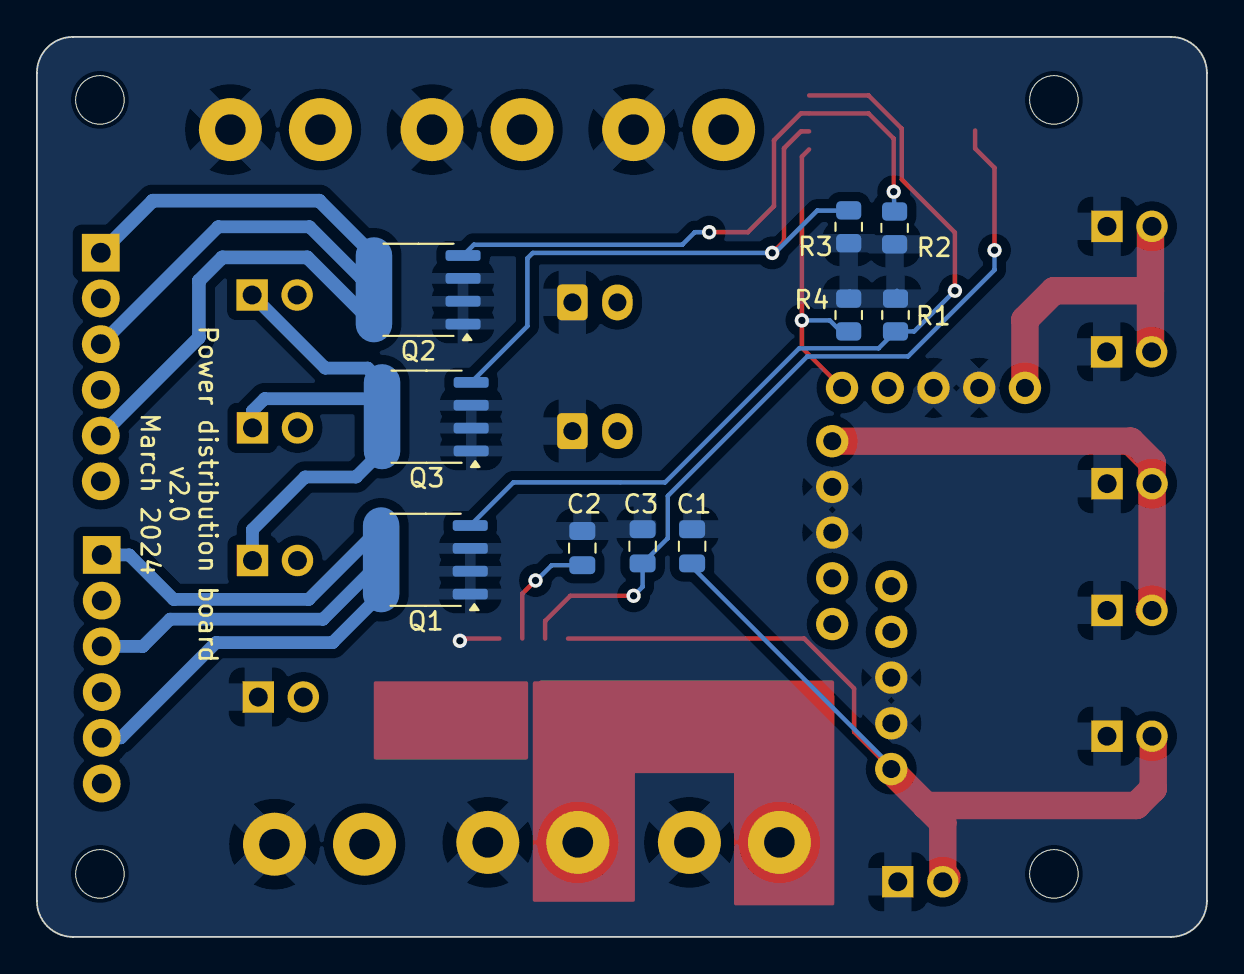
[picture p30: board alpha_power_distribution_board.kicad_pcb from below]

Board: 2 copper layers, 65.0 x 50.0 mm, 40 parts (10 on the bottom side), 15 nets.

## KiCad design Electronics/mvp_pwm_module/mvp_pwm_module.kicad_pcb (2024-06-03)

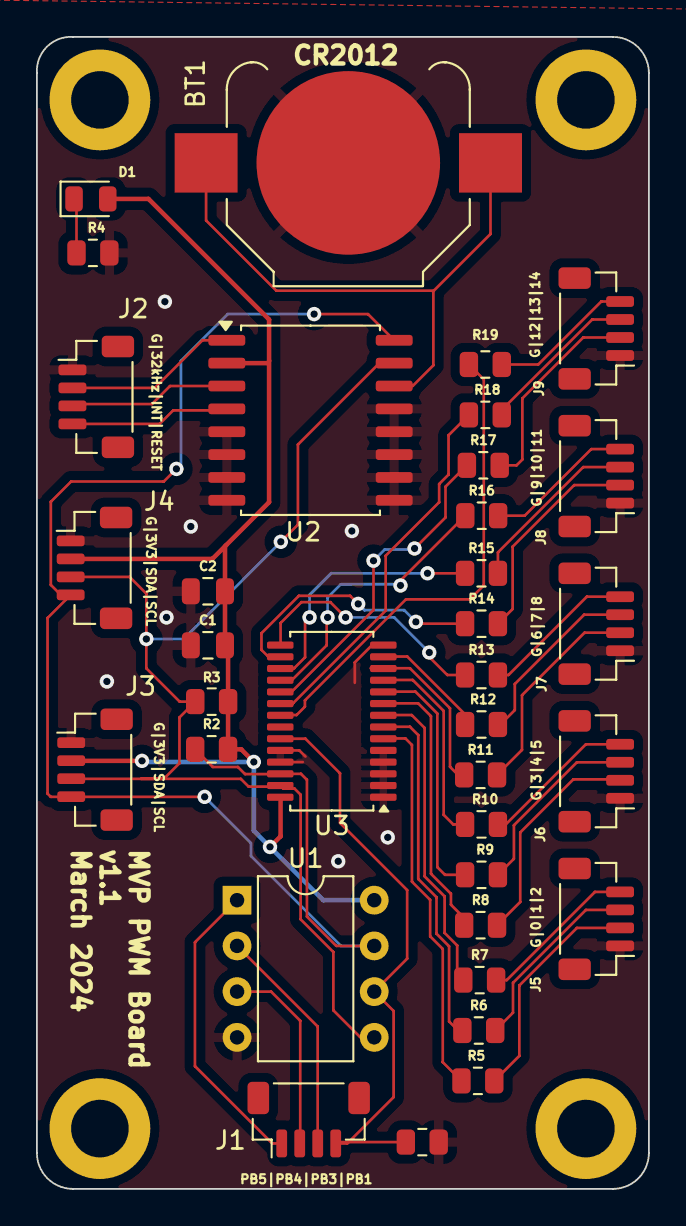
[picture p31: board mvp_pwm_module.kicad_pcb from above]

Board: 2 copper layers, 34.0 x 64.0 mm, 39 parts (0 on the bottom side), 43 nets.

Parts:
BT1: Battery_Cell; BatteryHolder_Keystone_3000_1x12mm
C1, C2: 10uF; C_0805_2012Metric
D1: LED; LED_0805_2012Metric
H1, H2, H3, H4: MountingHole; MountingHole_3.2mm_M3_DIN965_Pad
J1, J2: GPIO; JST_SH_BM04B-SRSS-TB_1x04-1MP_P1.00mm_Vertical
J3, J4: I2C; JST_SH_BM04B-SRSS-TB_1x04-1MP_P1.00mm_Vertical
J5: PWM0-1; JST_SH_BM04B-SRSS-TB_1x04-1MP_P1.00mm_Vertical
J6: PWM2-3; JST_SH_BM04B-SRSS-TB_1x04-1MP_P1.00mm_Vertical
J7: PWM4-5; JST_SH_BM04B-SRSS-TB_1x04-1MP_P1.00mm_Vertical
J8, J9: PWM6-7; JST_SH_BM04B-SRSS-TB_1x04-1MP_P1.00mm_Vertical
R1, R2, R3: 10k; R_0805_2012Metric
R4, R5, R6, R7, R8, R9, R10, R11, R12, R13, R14, R15, R16, R17, R18, R19: 220; R_0805_2012Metric
U1: ATtiny85-20P; DIP-8_W7.62mm
U2: DS3231M; SOIC-16W_7.5x10.3mm_P1.27mm
U3: PCA9685PW; TSSOP-28_4.4x9.7mm_P0.65mm

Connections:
3V3: C1.1, C2.1, D1.2 (A), J3.2, J4.2, R2.1, R3.1, U1.8 (VCC), U2.2 (VCC), U3.28 (VDD)
32KHz: J2.2, U2.1 (32KHZ)
GND: BT1.2 (-), C1.2, C2.2, J2.1, J3.1, J4.1, J5.1, J6.1, J7.1, J8.1, J9.1, R1.2, R4.2, U1.4 (GND), U2.5 (GND), U2.6 (GND), U2.7 (GND), U2.8 (GND), U2.9 (GND), U2.10 (GND), U2.11 (GND), U2.12 (GND), U2.13 (GND), U3.1 (A0), U3.2 (A1), U3.3 (A2), U3.4 (A3), U3.5 (A4), U3.14 (VSS), U3.24 (A5), U3.25 (EXTCLK)
I2C_SCL: J3.4, J4.4, R2.2, U1.7 (PB2), U2.16 (SCL), U3.26 (SCL)
I2C_SDA: J3.3, J4.3, R3.2, U1.5 (AREF/PB0), U2.15 (SDA), U3.27 (SDA)
INT_SQW: J2.3, U2.3 (~INT/SQW)
unnamed: BT1.1 (+), U2.14 (VBAT)
unnamed: D1.1 (K), R4.1
unnamed: R5.1, U3.6 (LED0)
unnamed: R6.1, U3.7 (LED1)
unnamed: R7.1, U3.8 (LED2)
unnamed: R8.1, U3.9 (LED3)
unnamed: R9.1, U3.10 (LED4)
unnamed: R10.1, U3.11 (LED5)
unnamed: R11.1, U3.12 (LED6)
unnamed: R12.1, U3.13 (LED7)
unnamed: R13.1, U3.15 (LED8)
unnamed: R14.1, U3.16 (LED9)
unnamed: R15.1, U3.17 (LED10)
unnamed: R16.1, U3.18 (LED11)
unnamed: R17.1, U3.19 (LED12)
unnamed: R18.1, U3.20 (LED13)
unnamed: R19.1, U3.21 (LED14)
PB1: J1.4, R1.1, U1.6 (PB1), U3.23 (~OE)
PB3: J1.3, U1.2 (XTAL1/PB3)
PB4: J1.2, U1.3 (XTAL2/PB4)
PB5: J1.1, U1.1 (~RESET/PB5)
PWM0: J5.2, R5.2
PWM1: J5.3, R6.2
PWM2: J5.4, R7.2
PWM3: J6.2, R8.2
PWM4: J6.3, R9.2
PWM5: J6.4, R10.2
PWM6: J7.2, R11.2
PWM7: J7.3, R12.2
PWM8: J7.4, R13.2
PWM9: J8.2, R14.2
PWM10: J8.3, R15.2
PWM11: J8.4, R16.2
PWM12: J9.2, R17.2
PWM13: J9.3, R18.2
PWM14: J9.4, R19.2
RTC_RESET: J2.4, U2.4 (~RST)

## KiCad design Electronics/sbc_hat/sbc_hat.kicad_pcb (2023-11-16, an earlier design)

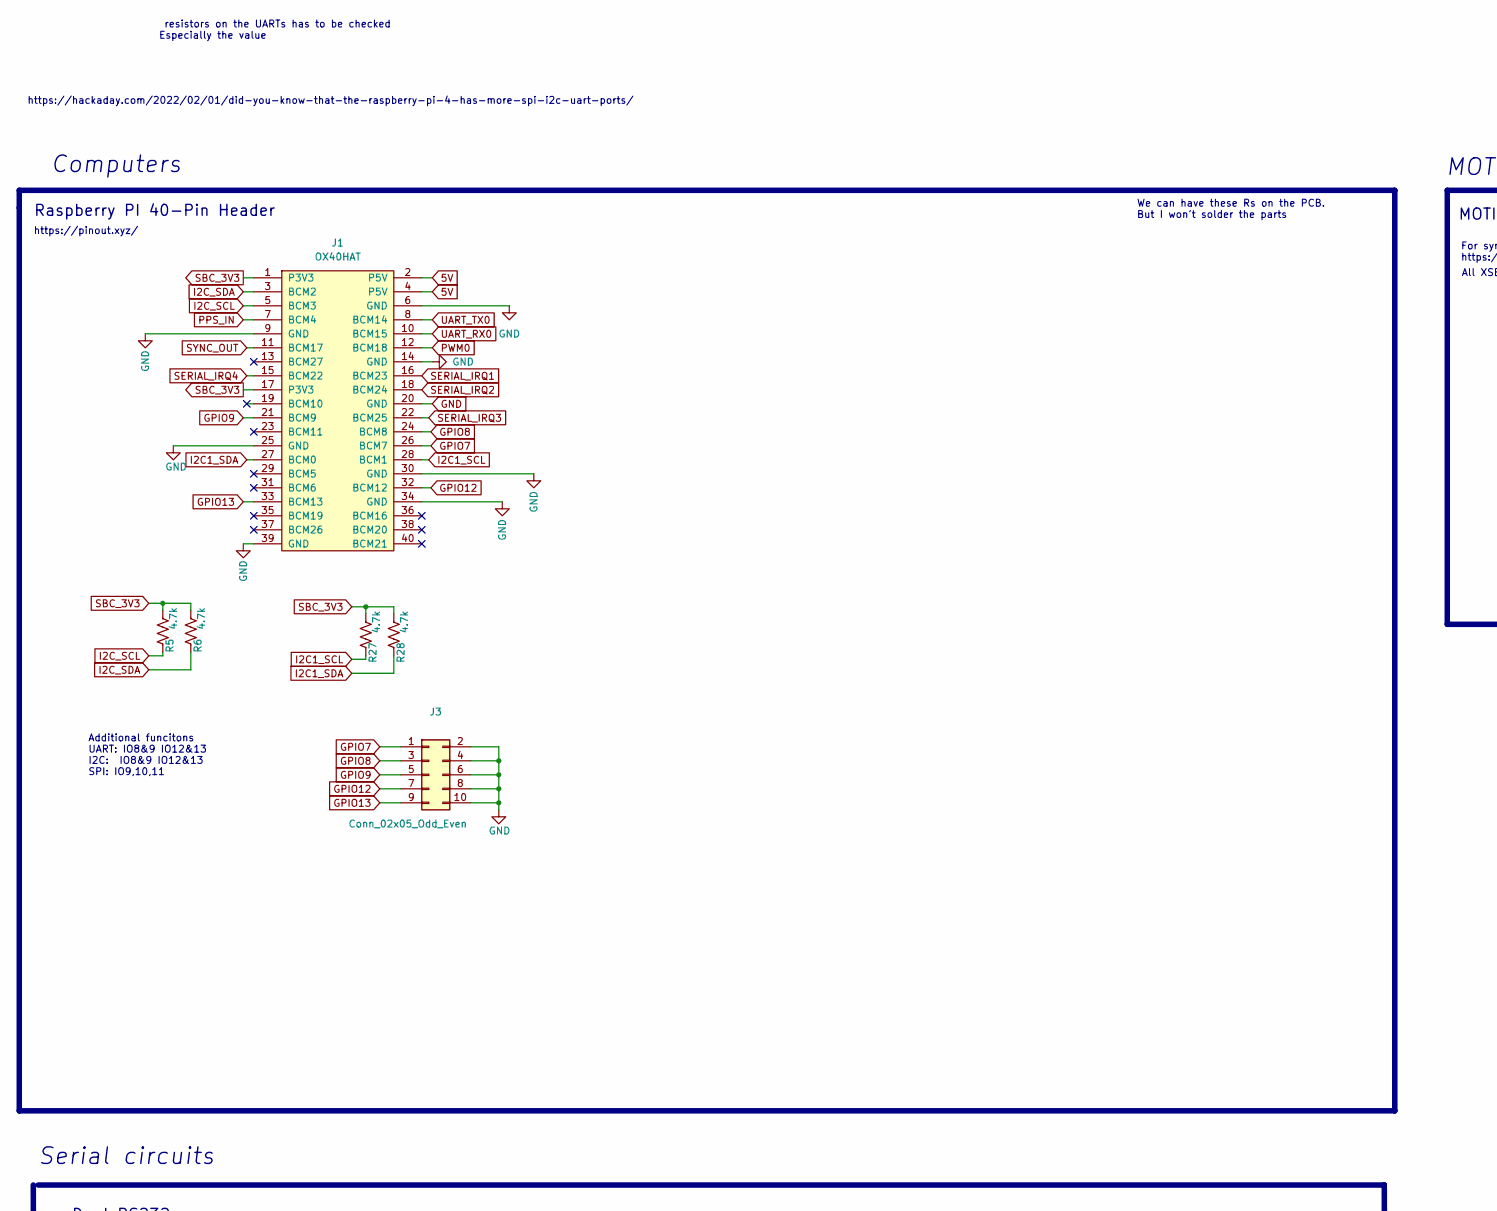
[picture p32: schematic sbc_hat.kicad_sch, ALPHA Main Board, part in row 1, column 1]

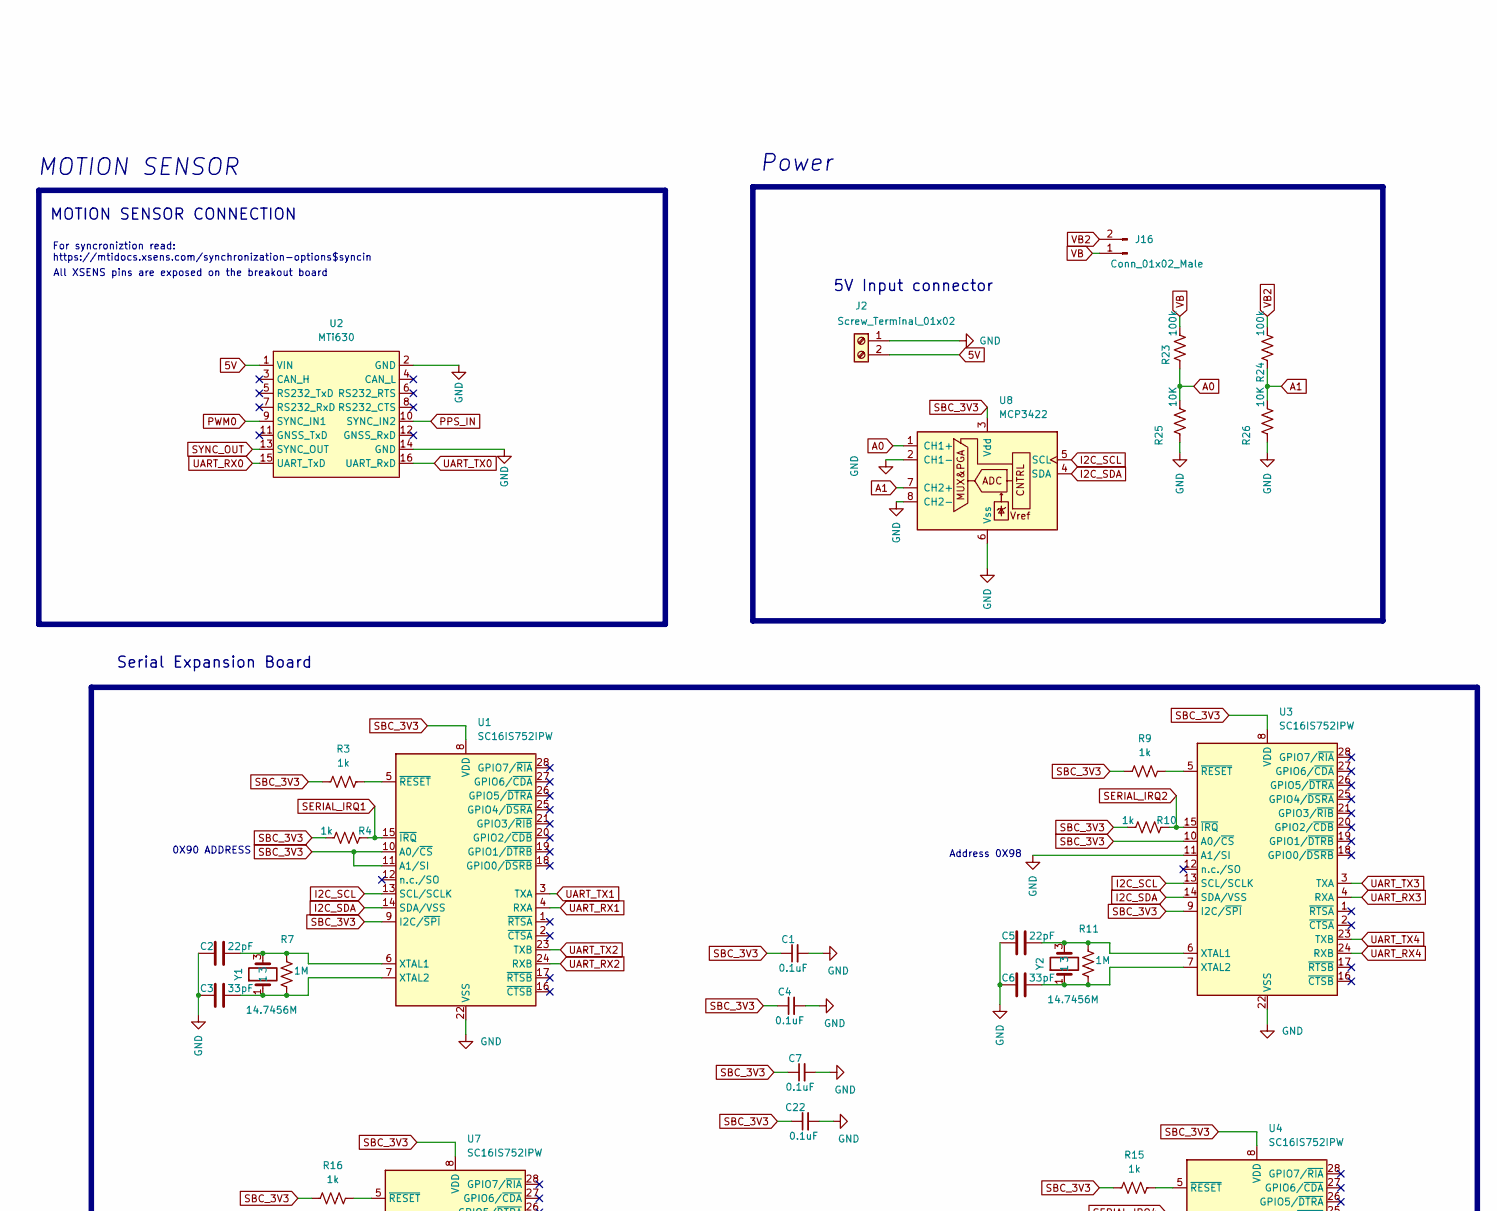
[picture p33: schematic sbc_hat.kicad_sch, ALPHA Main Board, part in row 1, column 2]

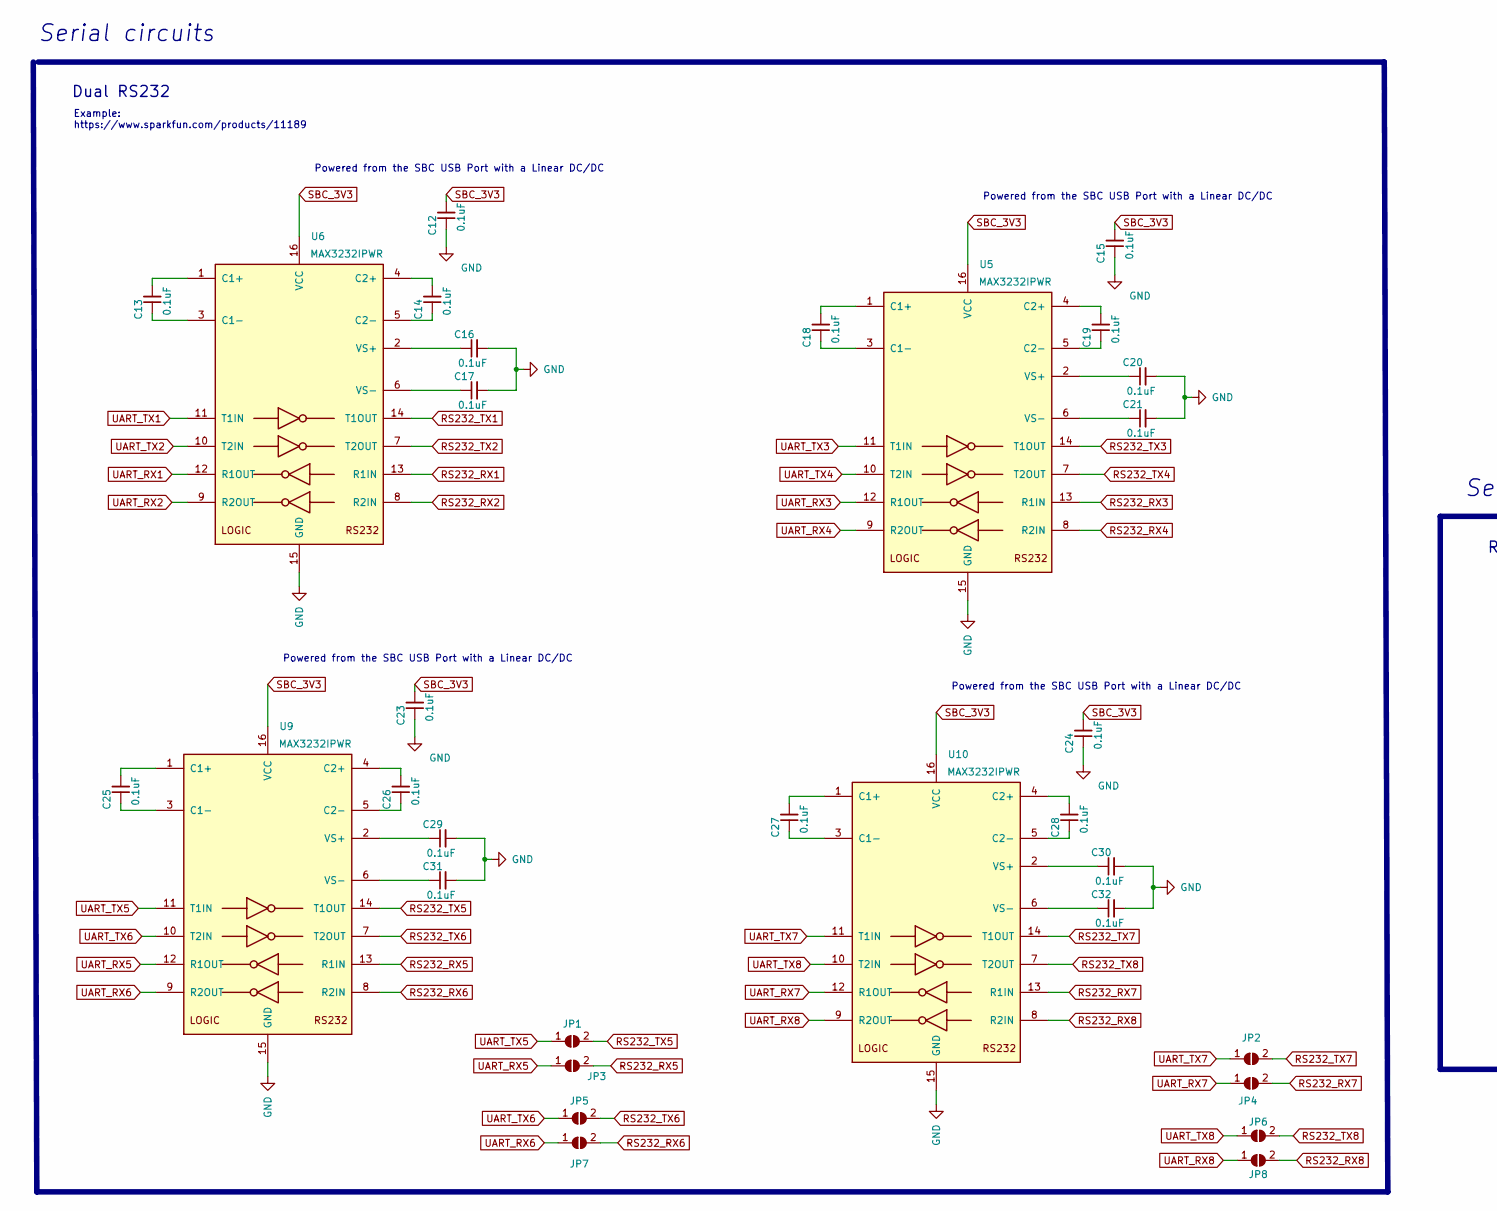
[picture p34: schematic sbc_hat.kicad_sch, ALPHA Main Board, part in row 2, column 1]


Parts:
C1, C4, C7, C12, C13, C14, C15, C16, C17, C18, C19, C20, C21, C22, C23, C24, C25, C26, C27, C28, C29, C30, C31, C32: 0.1uF; C_0805_2012Metric; Manufacturer_Part_Number 0805ZC104JAT2A; Digikey Part Number 478-11627-1-ND
C2, C5, C8, C9: 22pF; C_0805_2012Metric; Manufacturer_Part_Number 08055J220FBTTR; Digikey Part Number 478-11911-1-ND
C3, C6, C10, C11: 33pF; C_0805_2012Metric; Manufacturer_Part_Number 600F330FT250XT; Digikey Part Number 1284-1049-1-ND
J1: OX40HAT; PinSocket_2x20_P2.54mm_Vertical; Mouser Part Number 474-PRT-14017
J2: Screw_Terminal_01x02; TerminalBlock_Phoenix_MPT-0,5-2-2.54_1x02_P2.54mm_Horizontal; Manufacturer_Part_Number 1725656; Mouser Part Number 651-1725656
J3: Conn_02x05_Odd_Even; PinHeader_2x05_P2.54mm_Vertical
J4, J7, J14: RS232-1; JST_SH_BM04B-SRSS-TB_1x04-1MP_P1.00mm_Vertical; Manufacturer_Part_Number 4328; Digikey Part Number 1528-4328-ND
J5, J8, J15: RS232-2; JST_SH_BM04B-SRSS-TB_1x04-1MP_P1.00mm_Vertical; Manufacturer_Part_Number 4328; Digikey Part Number 1528-4328-ND
J6, J11: I2C-3; JST_SH_BM04B-SRSS-TB_1x04-1MP_P1.00mm_Vertical; Manufacturer_Part_Number 4328; Digikey Part Number 1528-4328-ND
J9: RS485-1; JST_SH_BM04B-SRSS-TB_1x04-1MP_P1.00mm_Vertical; Manufacturer_Part_Number 4328; Digikey Part Number 1528-4328-ND
J10: RS485-2; JST_SH_BM04B-SRSS-TB_1x04-1MP_P1.00mm_Vertical; Manufacturer_Part_Number 4328; Digikey Part Number 1528-4328-ND
J12: I2C-1; JST_SH_BM04B-SRSS-TB_1x04-1MP_P1.00mm_Vertical; Manufacturer_Part_Number 4328; Digikey Part Number 1528-4328-ND
J13: I2C-2; JST_SH_BM04B-SRSS-TB_1x04-1MP_P1.00mm_Vertical; Manufacturer_Part_Number 4328; Digikey Part Number 1528-4328-ND
J16: Conn_01x02_Male; PinHeader_1x02_P2.54mm_Vertical
JP1, JP2, JP3, JP4, JP5, JP6, JP7, JP8: SolderJumper_2_Open; SolderJumper-2_P1.3mm_Open_RoundedPad1.0x1.5mm
R3, R4, R9, R10, R15, R16, R17, R18: 1k; R_0805_2012Metric; Manufacturer_Part_Number 1-2176092-8; Digikey Part Number A110543CT-ND
R5, R6, R27, R28: 4.7k; R_0805_2012Metric; Manufacturer_Part_Number ERJ-T06J472V; Mouser Part Number 667-ERJ-T06J472V
R7, R11, R21, R22: 1M; R_0805_2012Metric; Manufacturer_Part_Number ERA-6AED105V; Mouser Part Number 667-ERA-6AED105V
R23, R24: 100k; R_0805_2012Metric; Manufacturer_Part_Number ERA-6AEB104V; Mouser Part Number 667-ERA-6AEB104V
R25, R26: 10K; R_0805_2012Metric; Manufacturer_Part_Number ERA-6AEB104V; Mouser Part Number 667-ERA-6AEB104V
U1, U3, U4, U7: SC16IS752IPW; TSSOP-28_4.4x9.7mm_P0.65mm
U2: MTi630
U5, U6, U9, U10: MAX3232IPWR; TSSOP-16_4.4x5mm_P0.65mm; Manufacturer_Part_Number MAX3232IPWR; Mouser Part Number 595-MAX3232IPWR
U8: MCP3422; SOIC-8-1EP_3.9x4.9mm_P1.27mm_EP2.29x3mm
Y1, Y2, Y3, Y4: 14.7456M; Crystal_SMD_3225-4Pin_3.2x2.5mm

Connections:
5V: J1.2 (P5V), J1.4 (P5V), J2.2, J4.2, J5.2, J7.2, J8.2, J9.2, J10.2, J14.2, J15.2, U2.1 (VIN)
A0: R23.2, R25.1, U8.1 (CH1+)
A1: R24.2, R26.1, U8.7 (CH2+)
GND: C1.2, C2.1, C3.1, C4.2, C5.1, C6.1, C7.2, C8.1, C9.1, C10.1, C11.1, C12.1, C15.1, C16.2, C17.2, C20.2, C21.2, C22.2, C23.1, C24.1, C29.2, C30.2, C31.2, C32.2, J1.6 (GND), J1.9 (GND), J1.14 (GND), J1.20 (GND), J1.25 (GND), J1.30 (GND), J1.34 (GND), J1.39 (GND), J2.1, J3.2, J3.4, J3.6, J3.8, J3.10, J4.1, J5.1, J6.1, J7.1, J8.1, J9.1, J10.1, J11.1, J12.1, J13.1, J14.1, J15.1, R25.2, R26.2, U1.22 (VSS), U2.2 (GND), U2.14 (GND), U3.11 (A1/SI), U3.22 (VSS), U4.10 (A0/~CS), U4.11 (A1/SI), U4.22 (VSS), U5.15 (GND), U6.15 (GND), U7.10 (A0/~CS), U7.22 (VSS), U8.2 (CH1-), U8.6 (Vss), U8.8 (CH2-), U9.15 (GND), U10.15 (GND)
GPIO7: J1.26 (BCM7), J3.1
GPIO8: J1.24 (BCM8), J3.3
GPIO9: J1.21 (BCM9), J3.5
GPIO12: J1.32 (BCM12), J3.7
GPIO13: J1.33 (BCM13), J3.9
I2C1_SCL: J1.28 (BCM1), J6.4, J11.4, R27.1
I2C1_SDA: J1.27 (BCM0), J6.3, J11.3, R28.1
I2C_SCL: J1.5 (BCM3), J12.4, J13.4, R5.1, U1.13 (SCL/SCLK), U3.13 (SCL/SCLK), U4.13 (SCL/SCLK), U7.13 (SCL/SCLK), U8.5 (SCL)
I2C_SDA: J1.3 (BCM2), J12.3, J13.3, R6.1, U1.14 (SDA/VSS), U3.14 (SDA/VSS), U4.14 (SDA/VSS), U7.14 (SDA/VSS), U8.4 (SDA)
unnamed: C2.2, R7.1, U1.6 (XTAL1), Y1.3
unnamed: C3.2, R7.2, U1.7 (XTAL2), Y1.1
unnamed: C5.2, R11.1, U3.6 (XTAL1), Y2.3
unnamed: C6.2, R11.2, U3.7 (XTAL2), Y2.1
unnamed: C8.2, R21.1, U4.6 (XTAL1), Y3.3
unnamed: C9.2, R22.1, U7.6 (XTAL1), Y4.3
unnamed: C10.2, R21.2, U4.7 (XTAL2), Y3.1
unnamed: C11.2, R22.2, U7.7 (XTAL2), Y4.1
unnamed: C13.1, U6.3 (C1-)
unnamed: C13.2, U6.1 (C1+)
unnamed: C14.1, U6.5 (C2-)
unnamed: C14.2, U6.4 (C2+)
unnamed: C16.1, U6.2 (VS+)
unnamed: C17.1, U6.6 (VS-)
unnamed: C18.1, U5.3 (C1-)
unnamed: C18.2, U5.1 (C1+)
unnamed: C19.1, U5.5 (C2-)
unnamed: C19.2, U5.4 (C2+)
unnamed: C20.1, U5.2 (VS+)
unnamed: C21.1, U5.6 (VS-)
unnamed: C25.1, U9.3 (C1-)
unnamed: C25.2, U9.1 (C1+)
unnamed: C26.1, U9.5 (C2-)
unnamed: C26.2, U9.4 (C2+)
unnamed: C27.1, U10.3 (C1-)
unnamed: C27.2, U10.1 (C1+)
unnamed: C28.1, U10.5 (C2-)
unnamed: C28.2, U10.4 (C2+)
unnamed: C29.1, U9.2 (VS+)
unnamed: C30.1, U10.2 (VS+)
unnamed: C31.1, U9.6 (VS-)
unnamed: C32.1, U10.6 (VS-)
unnamed: R3.2, U1.5 (~RESET)
unnamed: R9.2, U3.5 (~RESET)
unnamed: R15.2, U4.5 (~RESET)
unnamed: R16.2, U7.5 (~RESET)
PPS_IN: J1.7 (BCM4), U2.10 (SYNC_IN2)
PWM0: J1.12 (BCM18), U2.9 (SYNC_IN1)
RS232_RX1: J14.4, U6.13 (R1IN)
RS232_RX2: J15.4, U6.8 (R2IN)
RS232_RX3: J9.4, U5.13 (R1IN)
RS232_RX4: J10.4, U5.8 (R2IN)
RS232_RX5: J4.4, JP3.2 (B), U9.13 (R1IN)
RS232_RX6: J5.4, JP7.2 (B), U9.8 (R2IN)
RS232_RX7: J7.4, JP4.2 (B), U10.13 (R1IN)
RS232_RX8: J8.4, JP8.2 (B), U10.8 (R2IN)
RS232_TX1: J14.3, U6.14 (T1OUT)
RS232_TX2: J15.3, U6.7 (T2OUT)
RS232_TX3: J9.3, U5.14 (T1OUT)
RS232_TX4: J10.3, U5.7 (T2OUT)
RS232_TX5: J4.3, JP1.2 (B), U9.14 (T1OUT)
RS232_TX6: J5.3, JP5.2 (B), U9.7 (T2OUT)
RS232_TX7: J7.3, JP2.2 (B), U10.14 (T1OUT)
RS232_TX8: J8.3, JP6.2 (B), U10.7 (T2OUT)
SBC_3V3: C1.1, C4.1, C7.1, C12.2, C15.2, C22.1, C23.2, C24.2, J1.1 (P3V3), J1.17 (P3V3), J6.2, J11.2, J12.2, J13.2, R3.1, R4.2, R5.2, R6.2, R9.1, R10.2, R15.1, R16.1, R17.2, R18.2, R27.2, R28.2, U1.8 (VDD), U1.9 (I2C/~SPI), U1.10 (A0/~CS), U1.11 (A1/SI), U3.8 (VDD), U3.9 (I2C/~SPI), U3.10 (A0/~CS), U4.8 (VDD), U4.9 (I2C/~SPI), U5.16 (VCC), U6.16 (VCC), U7.8 (VDD), U7.9 (I2C/~SPI), U7.11 (A1/SI), U8.3 (Vdd), U9.16 (VCC), U10.16 (VCC)
SERIAL_IRQ1: J1.16 (BCM23), R4.1, U1.15 (~IRQ)
SERIAL_IRQ2: J1.18 (BCM24), R10.1, U3.15 (~IRQ)
SERIAL_IRQ3: J1.22 (BCM25), R18.1, U7.15 (~IRQ)
SERIAL_IRQ4: J1.15 (BCM22), R17.1, U4.15 (~IRQ)
SYNC_OUT: J1.11 (BCM17), U2.13 (SYNC_OUT)
UART_RX0: J1.10 (BCM15), U2.15 (UART_TxD)
UART_RX1: U1.4 (RXA), U6.12 (R1OUT)
UART_RX2: U1.24 (RXB), U6.9 (R2OUT)
UART_RX3: U3.4 (RXA), U5.12 (R1OUT)
UART_RX4: U3.24 (RXB), U5.9 (R2OUT)
UART_RX5: JP3.1 (A), U7.4 (RXA), U9.12 (R1OUT)
UART_RX6: JP7.1 (A), U7.24 (RXB), U9.9 (R2OUT)
UART_RX7: JP4.1 (A), U4.4 (RXA), U10.12 (R1OUT)
UART_RX8: JP8.1 (A), U4.24 (RXB), U10.9 (R2OUT)
UART_TX0: J1.8 (BCM14), U2.16 (UART_RxD)
UART_TX1: U1.3 (TXA), U6.11 (T1IN)
UART_TX2: U1.23 (TXB), U6.10 (T2IN)
UART_TX3: U3.3 (TXA), U5.11 (T1IN)
UART_TX4: U3.23 (TXB), U5.10 (T2IN)
UART_TX5: JP1.1 (A), U7.3 (TXA), U9.11 (T1IN)
UART_TX6: JP5.1 (A), U7.23 (TXB), U9.10 (T2IN)
UART_TX7: JP2.1 (A), U4.3 (TXA), U10.11 (T1IN)
UART_TX8: JP6.1 (A), U4.23 (TXB), U10.10 (T2IN)
VB: J16.1, R23.1
VB2: J16.2, R24.1

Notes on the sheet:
I2C Connections
Powered from the SBC USB Port with a Linear DC/DC
0X90 ADDRESS
5V Input connector
RS232
Serial circuits
MOTION SENSOR CONNECTION
Dual RS232
Power
Address 0X9A
Example: https://www.sparkfun.com/products/11189
Additional funcitons UART: IO8&9 IO12&13 I2C: IO8&9 IO12&13 SPI: IO9,10,11
All XSENS pins are exposed on the breakout board
Computers
0X92 ADDRESS
For syncroniztion read: https://mtidocs.xsens.com/synchronization-options$syncin
We can have these Rs on the PCB. But I won't solder the parts
https://pinout.xyz/
Raspberry PI 40-Pin Header
https://hackaday.com/2022/02/01/did-you-know-that-the-raspberry-pi-4-has-more-spi-i2c-uart-ports/
MOTION SENSOR
resistors on the UARTs has to be checked Especially the value
Address 0X98
Serial Expansion Board
Serial and I2C ports



Board: 2 copper layers, 85.0 x 56.0 mm, 94 parts (9 on the bottom side), 93 nets.

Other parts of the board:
MH1, MH2, MH3, MH4: MountingHole_2.7mm_M2.5

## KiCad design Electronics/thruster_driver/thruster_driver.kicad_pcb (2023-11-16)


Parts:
C1, C2: 1uf; C_0805_2012Metric; Manufacturer_Part_Number 0805YC106KAT2A; Mouser Part Number 581-0805YC106KAT2A
C3, C4, C5, C6, C7: 0.1uF; C_0805_2012Metric; Manufacturer_Part_Number 0805ZC104JAT2A; Digikey Part Number 478-11627-1-ND
H1, H2: MountingHole; MountingHole_2.2mm_M2_ISO7380_Pad
J1: MICROMOD-2222-C; M.2-CONNECTOR-E; Manufacturer_Part_Number KIT-16549; Digikey Part Number 1568-KIT-16549-ND
J2: RS232; JST_SH_BM04B-SRSS-TB_1x04-1MP_P1.00mm_Vertical; Manufacturer_Part_Number 4328; Digikey Part Number 1528-4328-ND
J3: PWM01; JST_SH_BM04B-SRSS-TB_1x04-1MP_P1.00mm_Vertical; Manufacturer_Part_Number 4328; Digikey Part Number 1528-4328-ND
J4: PWM23; JST_SH_BM04B-SRSS-TB_1x04-1MP_P1.00mm_Vertical; Manufacturer_Part_Number 4328; Digikey Part Number 1528-4328-ND
J5: I2C; JST_SH_BM04B-SRSS-TB_1x04-1MP_P1.00mm_Vertical; Manufacturer_Part_Number 4328; Digikey Part Number 1528-4328-ND
J6: PWM45; JST_SH_BM04B-SRSS-TB_1x04-1MP_P1.00mm_Vertical; Manufacturer_Part_Number 4328; Digikey Part Number 1528-4328-ND
J7: RS485; JST_SH_BM04B-SRSS-TB_1x04-1MP_P1.00mm_Vertical; Manufacturer_Part_Number 4328; Digikey Part Number 1528-4328-ND
J8, J9: Conn_01x03_Male; PinHeader_1x03_P2.54mm_Vertical
J10: USB_B_Micro; USB_Micro-B_Amphenol_10118194_Horizontal; Manufacturer_Part_Number 10118194-0001LF; Digikey Part Number 609-4618-2-ND
R1, R2: 4.7k; R_0805_2012Metric; Manufacturer_Part_Number ERJ-T06J472V; Mouser Part Number 667-ERJ-T06J472V
R4: 100k; R_0805_2012Metric; Manufacturer_Part_Number ERJ-T06J472V; Mouser Part Number 667-ERJ-T06J472V
R5: 10k; R_0805_2012Metric; Manufacturer_Part_Number ERJ-T06J472V; Mouser Part Number 667-ERJ-T06J472V
SW1, SW2: EVQ-P2602W; SW_SPST_EVQP2
U1: AP2112K-3.3; SOT-23-5
U2: MAX3232IPWR; TSSOP-16_4.4x5mm_P0.65mm; Manufacturer_Part_Number MAX3232IPWR; Mouser Part Number 595-MAX3232IPWR

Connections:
3v3: C2.2, C3.2, J1.2 (3.3V), J1.74 (3.3V), J2.2, J5.2, J7.2, J8.1, R1.1, R2.1, U1.5 (VOUT), U2.16 (VCC)
5V: C1.2, J1.9 (USB_VIN), J10.1 (VBUS), U1.1 (VIN), U1.3 (EN)
A0: J1.34 (A0), R4.1, R5.2
BOOT: J1.11 (~BOOT), SW2.1 (C); also elsewhere on the board
GND: C1.1, C2.1, C3.1, C6.2, C7.2, J1.1 (GND), J1.7 (GND), J1.33 (GND), J1.36 (GND), J1.39 (GND), J1.45 (GND), J1.75 (GND), J2.1, J3.1, J3.2, J4.1, J4.2, J5.1, J6.1, J6.2, J7.1, J8.2, J9.1, J10.5 (GND), J10.6 (Shield), R5.1, SW1.2 (D), SW2.2 (D), U1.2 (GND), U2.15 (GND); also elsewhere on the board
GPIO8: J1.67 (G8), J9.2
GPIO11: J1.8 (G11), J9.3
I2C_SCL: J1.14 (I2C_SCL), J5.4, R1.2
I2C_SDA: J1.12 (I2C_SDA), J5.3, R2.2
unnamed: C4.1, U2.3 (C1-)
unnamed: C4.2, U2.1 (C1+)
unnamed: C5.1, U2.5 (C2-)
unnamed: C5.2, U2.4 (C2+)
unnamed: C6.1, U2.2 (VS+)
unnamed: C7.1, U2.6 (VS-)
PWM0: J1.32 (PWM0), J3.4
PWM1: J1.47 (PWM1), J3.3
PWM2: J1.40 (G0/BUS0), J4.4
PWM3: J1.44 (G2/BUS2), J4.3
PWM4: J1.48 (G4/BUS4), J6.4
PWM5: J1.71 (G6/BUS6), J6.3
RESET: J1.6 (~RESET), SW1.1 (C); also elsewhere on the board
RS232_RX1: J7.4, U2.8 (R2IN)
RS232_RX2: J2.4, U2.13 (R1IN)
RS232_TX1: J7.3, U2.7 (T2OUT)
RS232_TX2: J2.3, U2.14 (T1OUT)
UART_RX1: J1.19 (RX1), U2.9 (R2OUT)
UART_RX2: J1.20 (RX2), U2.12 (R1OUT)
UART_TX1: J1.17 (TX1), U2.10 (T2IN)
UART_TX2: J1.22 (TX2), U2.11 (T1IN)
USB_D+: J1.3 (USB_D+), J10.3 (D+)
USB_D-: J1.5 (USB_D-), J10.2 (D-)
VB: J8.3, R4.2

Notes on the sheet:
I2C Pull-up Resistors
Dual RS232
Example: https://www.sparkfun.com/products/11189


Board: 2 copper layers, 45.0 x 31.0 mm, 27 parts (0 on the bottom side), 33 nets.

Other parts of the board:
Boot: EVQ-P2602W; SW_SPST_EVQP2
REST: EVQ-P2602W; SW_SPST_EVQP2

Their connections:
BOOT: Boot.1 (C); also elsewhere on the board
GND: Boot.2 (D), REST.2 (D); also elsewhere on the board
RESET: REST.1 (C); also elsewhere on the board

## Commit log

2023-09-07 electronics release 1.0
    [022232021.stp, RISE_battery_power_distribution.kicad_pcb, RISE_battery_power_distribution.kicad_sch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]
2023-09-07 added pdf
    [alpha_power_distribution_board.kicad_sch]
2023-09-07 alpha auv stand step file uploaded
    [AUV_stand.step]
2023-09-09 uploaded frame and vertical thruster
2023-09-10 Updated fairing cad folder
    [S1.step, S2.step, S3.step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]
2023-09-10 put schematics into a folder
2023-09-10 update schematics links
2023-09-10 updated surge thruster and lifting plate
    [lifting_plate.step]
2023-09-10 Added ping360 and dvl plate information
    [DVL_plate.step, Ping360_assembly.step]
2023-09-10 add subfolders
    [DVL_plate.step, Ping360_assembly.step, S1.step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]
2023-09-10 Added part list and updated part number
    [ALPHA_Parts_list.xlsx, AUV_stand.step, DVL_plate.step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]
2023-10-15 Updated pcb
2023-10-15 Added electronics diagrams for endcap and internal housing
2023-11-16 updated power distribuiotn and esc board
    [sbc_hat.kicad_pcb, sbc_hat.kicad_sch, thruster_driver.kicad_pcb]
2024-06-03 added three new boards, and readme files
    [ESC_board.kicad_pcb, ESC_board.kicad_sch, alpha_power_distribution_board.kicad_pcb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]
2024-09-20 update electronics files to the newest version
    [022232021.stp, ESC_board.kicad_pcb, ESC_board.kicad_sch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]
